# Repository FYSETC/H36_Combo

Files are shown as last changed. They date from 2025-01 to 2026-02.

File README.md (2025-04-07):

# H36_Combo
H36 Combo V1 is a newly designed 125℃ high temperature tool board Based on STMG0B1T3.

> [!IMPORTANT] 
>- Since there is no 125 degree Celsius USB-HUB chip, the 125 degree Celsius operating environment is limited to CANBUS mode；
>- Klipper currently does not support 125 degree Celsius accelerometers, so the 125 degree Celsius operating environment does not include accelerometers. The default version of H36 is ADXL345, which has a maximum operating temperature of 85 degrees Celsius. The 105 degree Celsius ADXL345-EP version is optional, but it is more expensive.

V1.1

1.add Driver NTC

2.add 3.3V/5v monitor

3.add 24v monitor

\-------------------------------------

V1.2

1.change to XT30

2.add reserve protection

3.fix can/usb indicate

\-------------------------------------

V1.3 (Currently Available)

> [!NOTE]
> V1.3 only makes hardware changes and does not affect any software configuration.

1.Add level_shift to FAN_TACH

2.Fix silk mark

3.Add jumper resistor from USB-C to STM32

4.ADXL345-EP optional

5.Change the LDO chip to TLV75733

6.New mass-produced cables（Mold Forming）

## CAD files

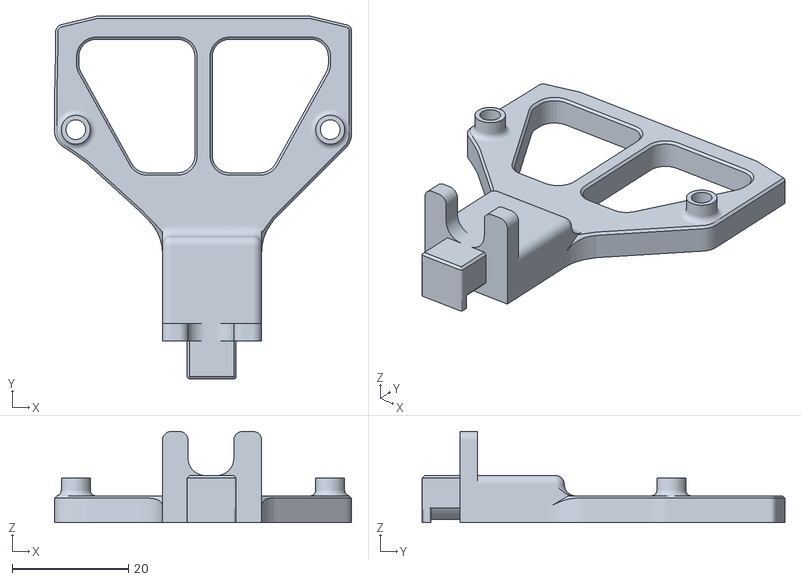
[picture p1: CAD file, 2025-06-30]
STL/H36_MainMount_FYS_Assembly.STL
51.2 x 62.5 x 15.7

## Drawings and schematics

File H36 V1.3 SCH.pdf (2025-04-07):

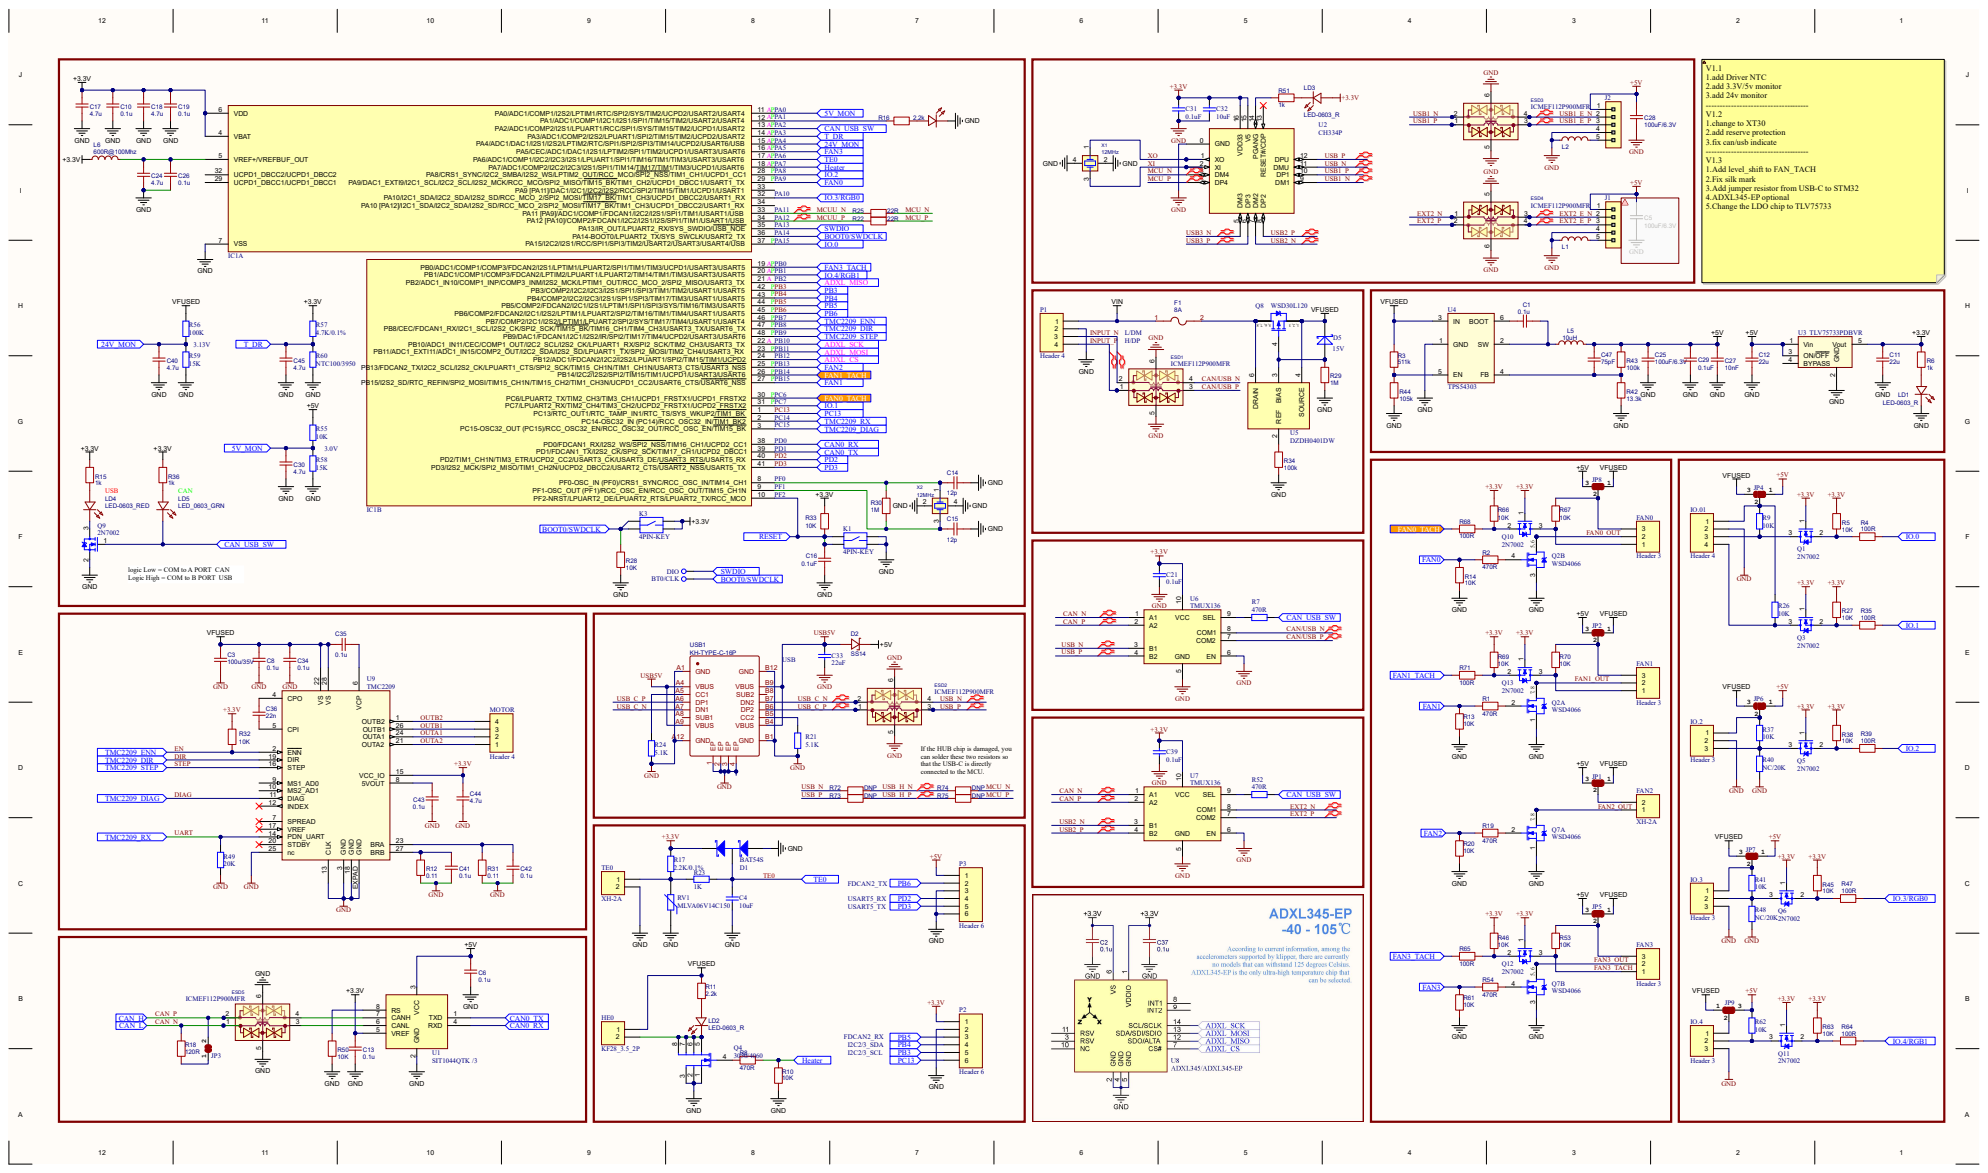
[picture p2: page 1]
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

logic Low = COM to A PORT CAN
Logic High = COM to B PORT USB

If the HUB chip is damaged, you
can solder these two resistors so
that the USB-C is directly
connected to the MCU.

According to current information, among the

accelerometers supported by klipper, there are currently
no models that can withstand 125 degrees Celsius.
ADXL345-EP is the only ultra-high temperature chip that

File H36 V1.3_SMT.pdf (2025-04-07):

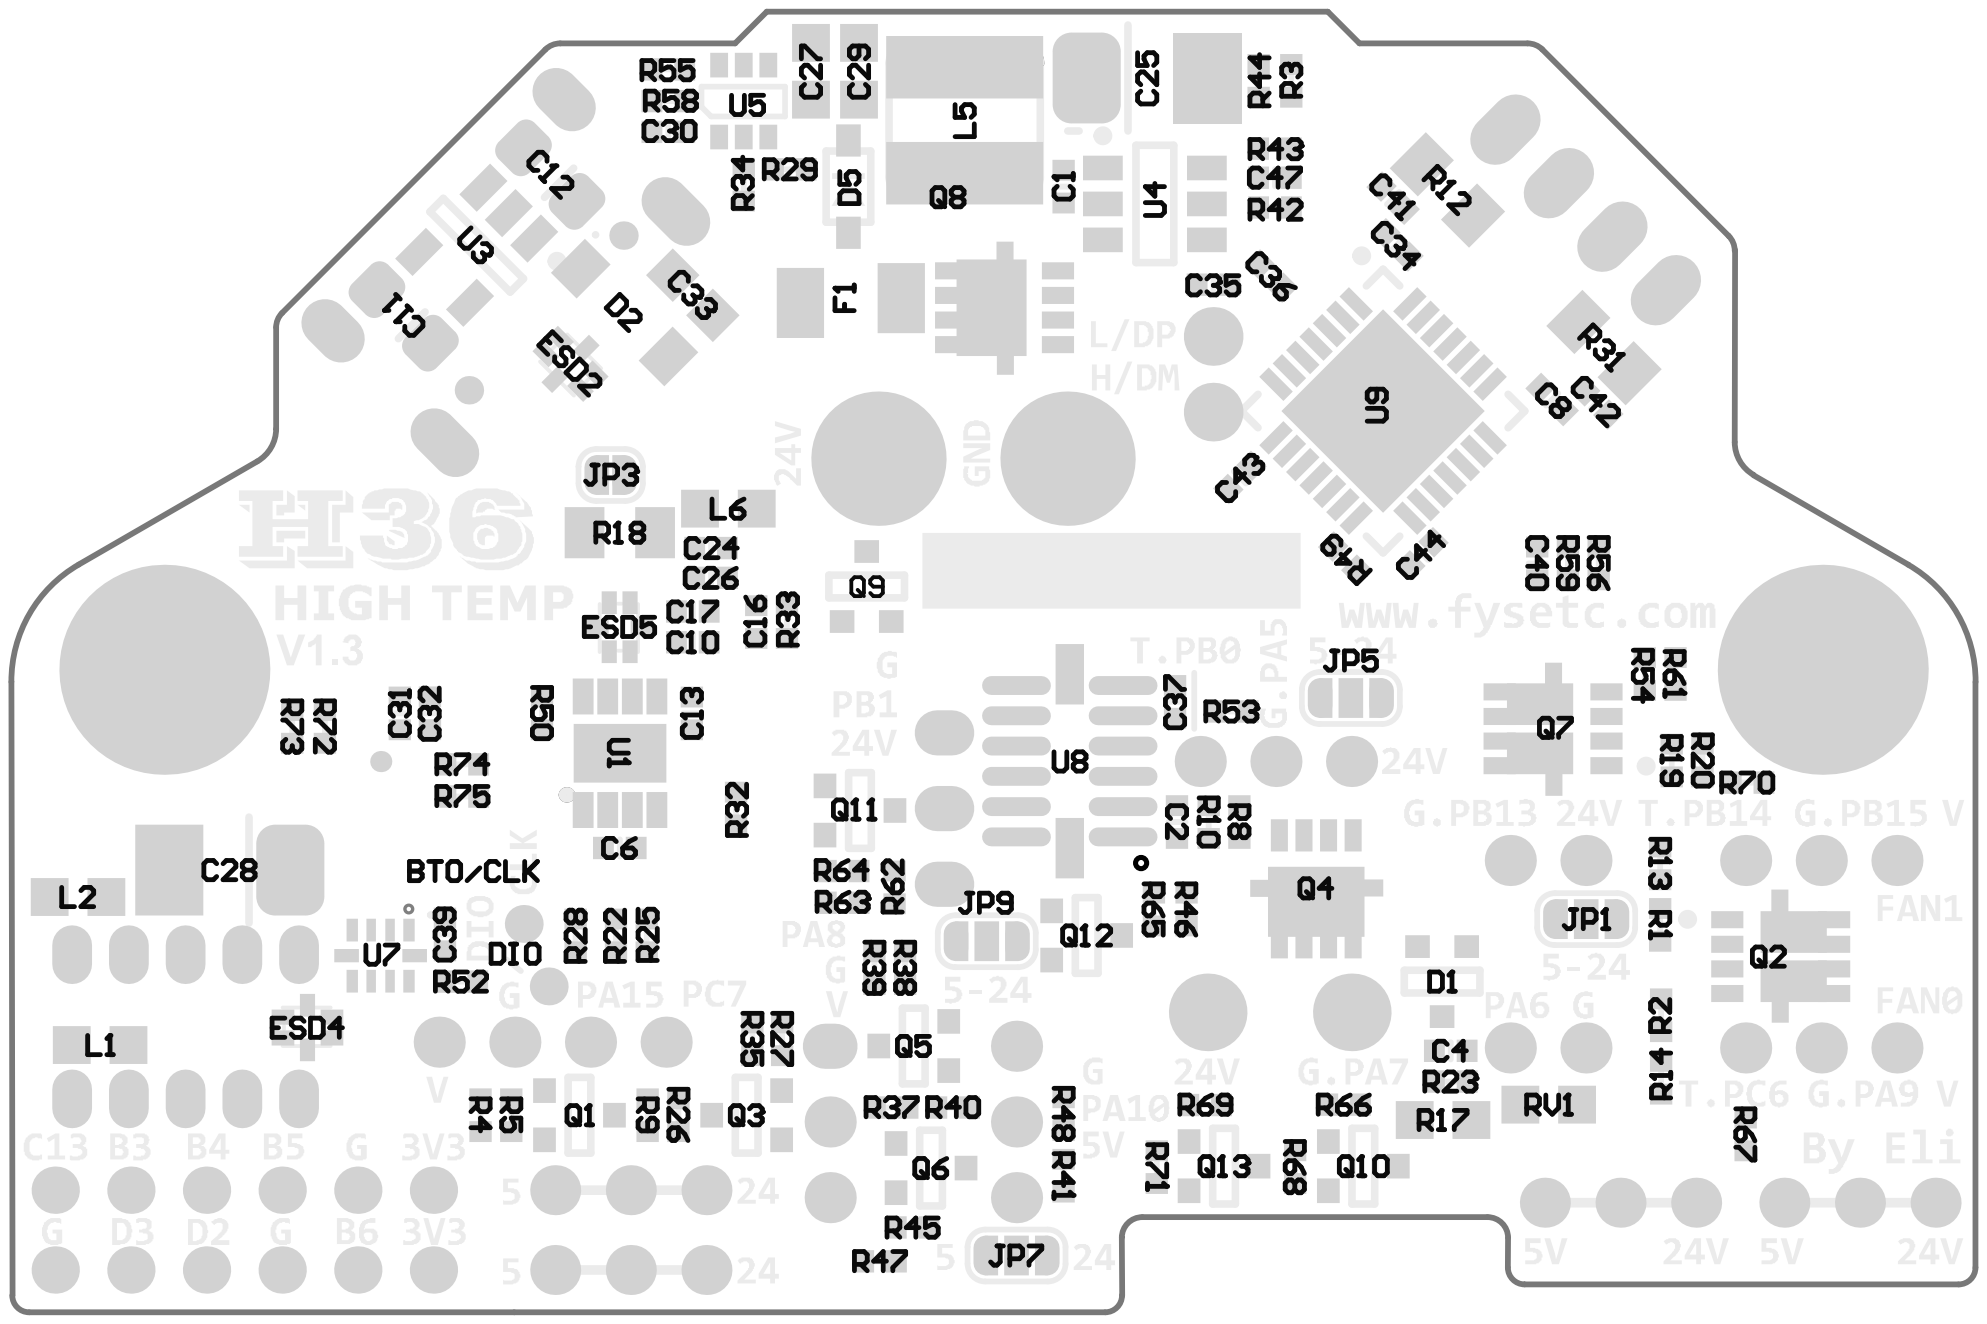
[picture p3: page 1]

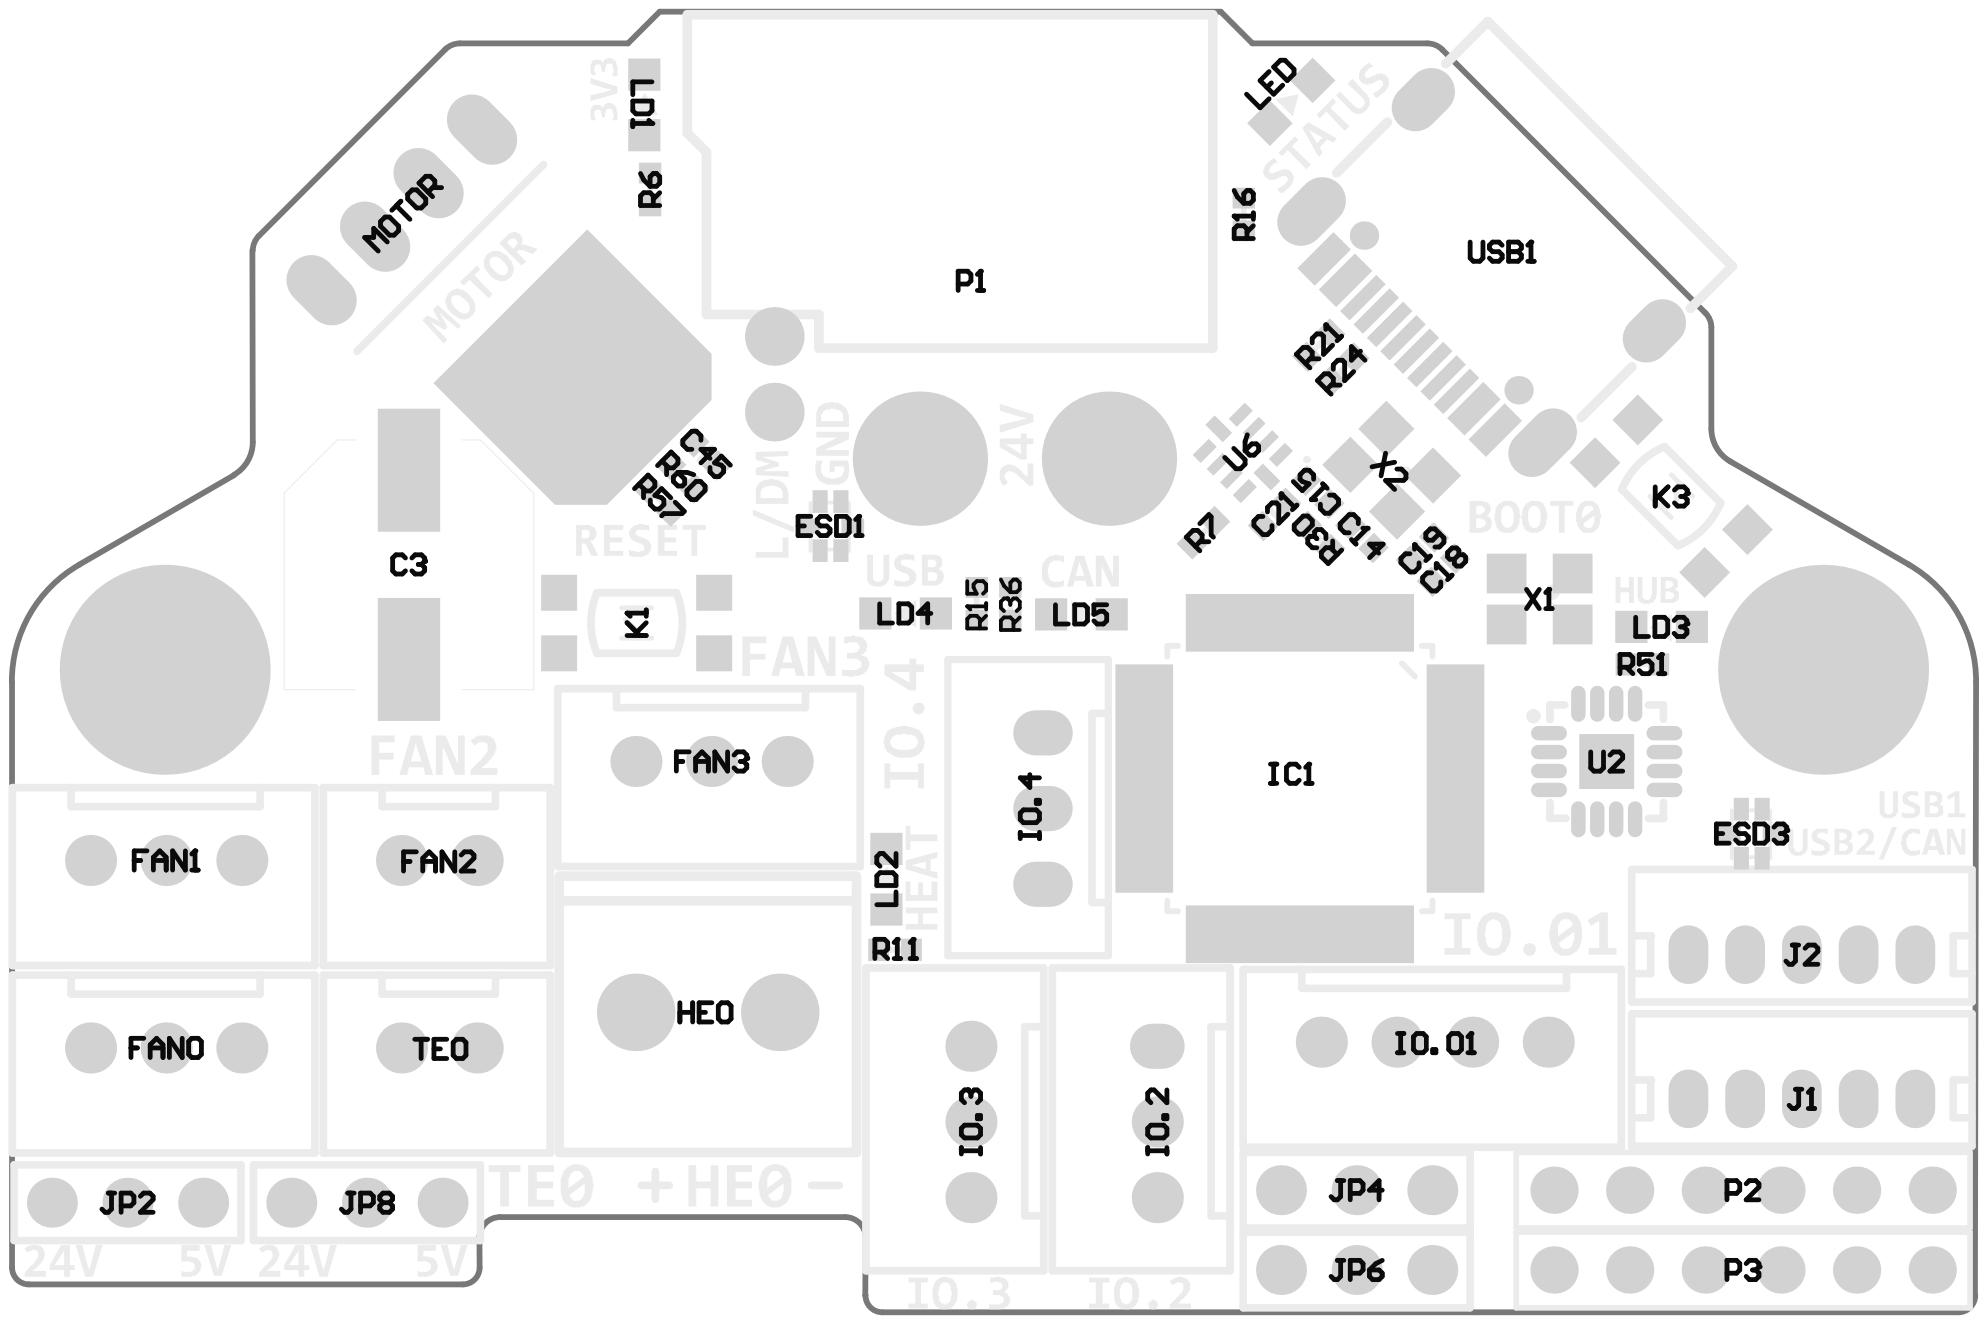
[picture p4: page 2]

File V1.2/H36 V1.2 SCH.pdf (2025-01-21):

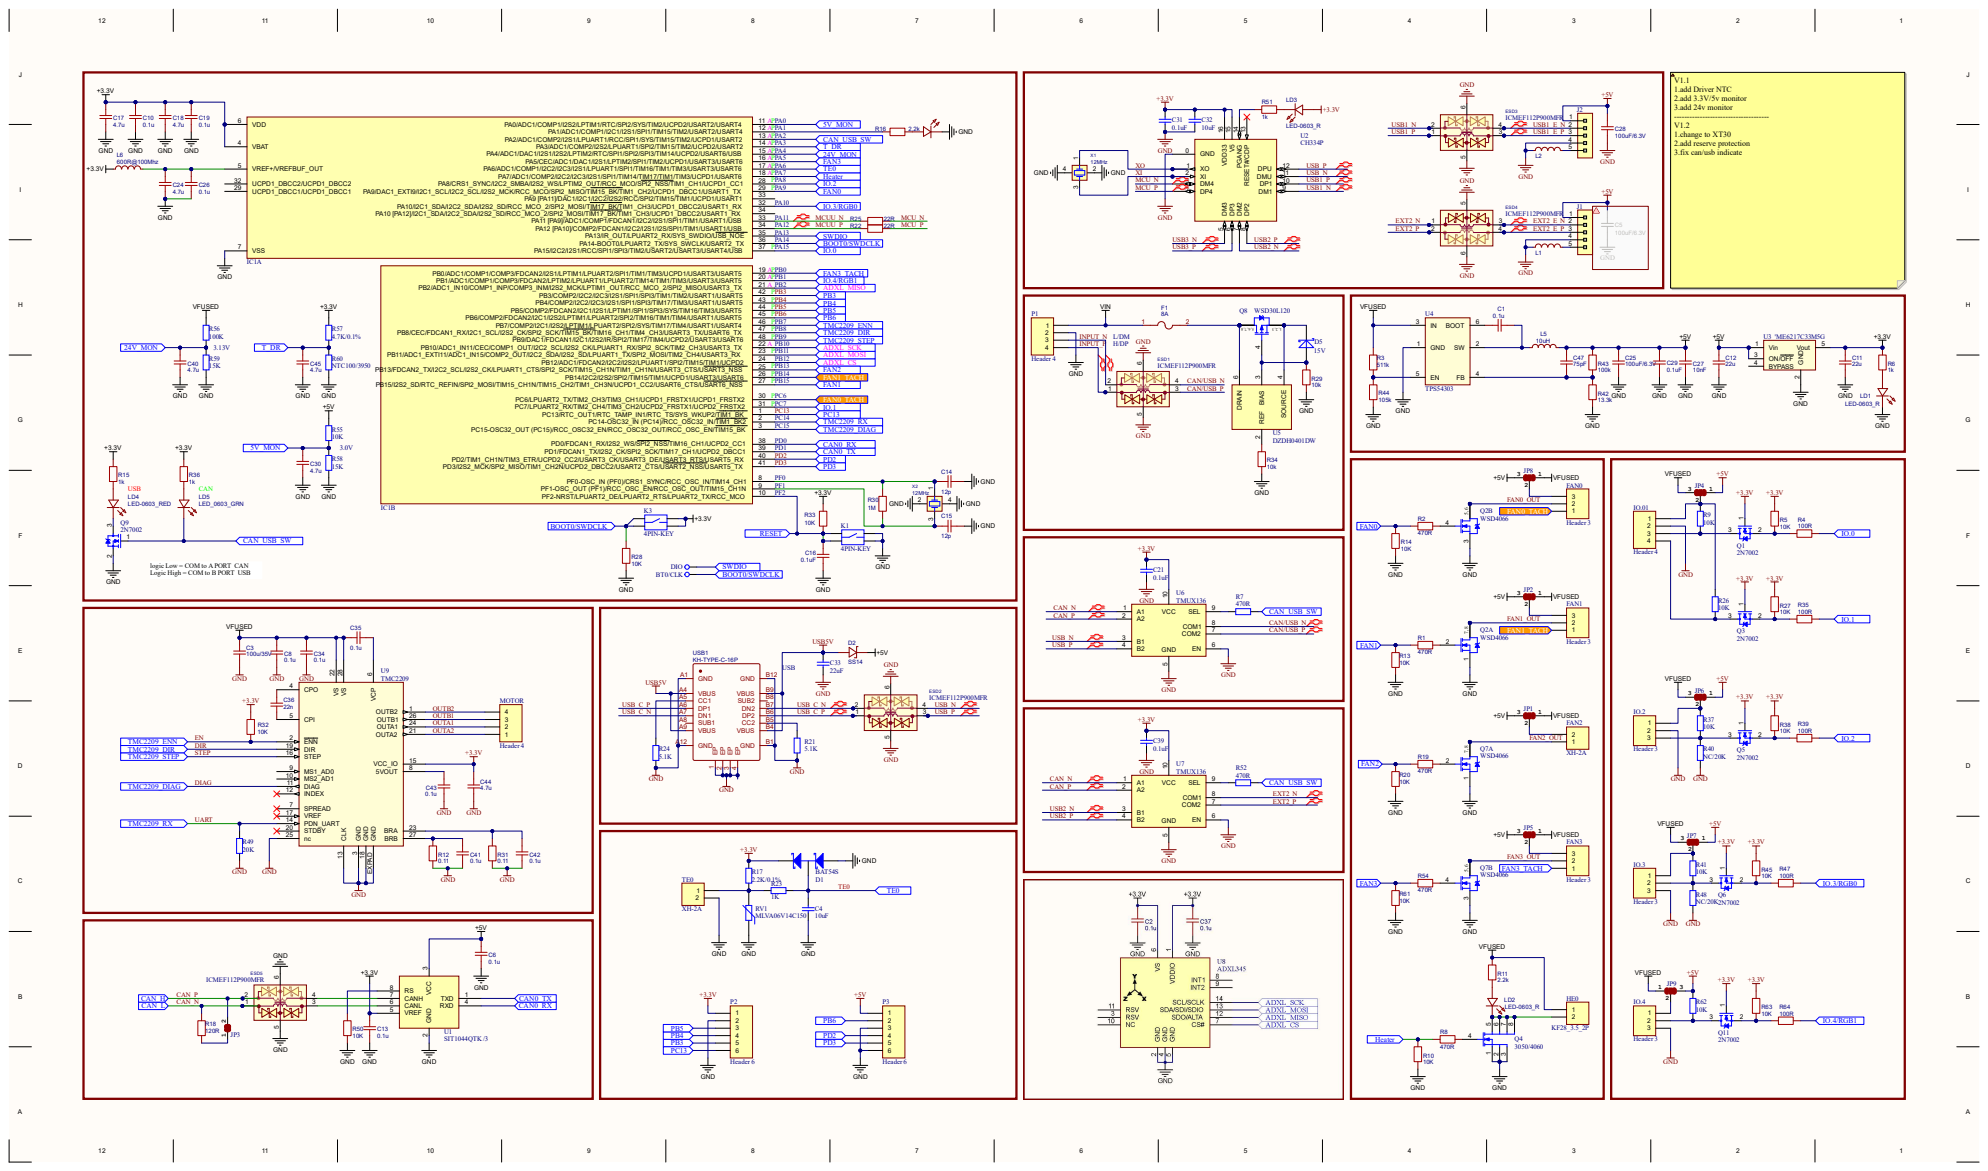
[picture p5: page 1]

1.change to XT30
2.add reserve protection
3.fix can/usb indicate

logic Low = COM to A PORT CAN
Logic High = COM to B PORT USB

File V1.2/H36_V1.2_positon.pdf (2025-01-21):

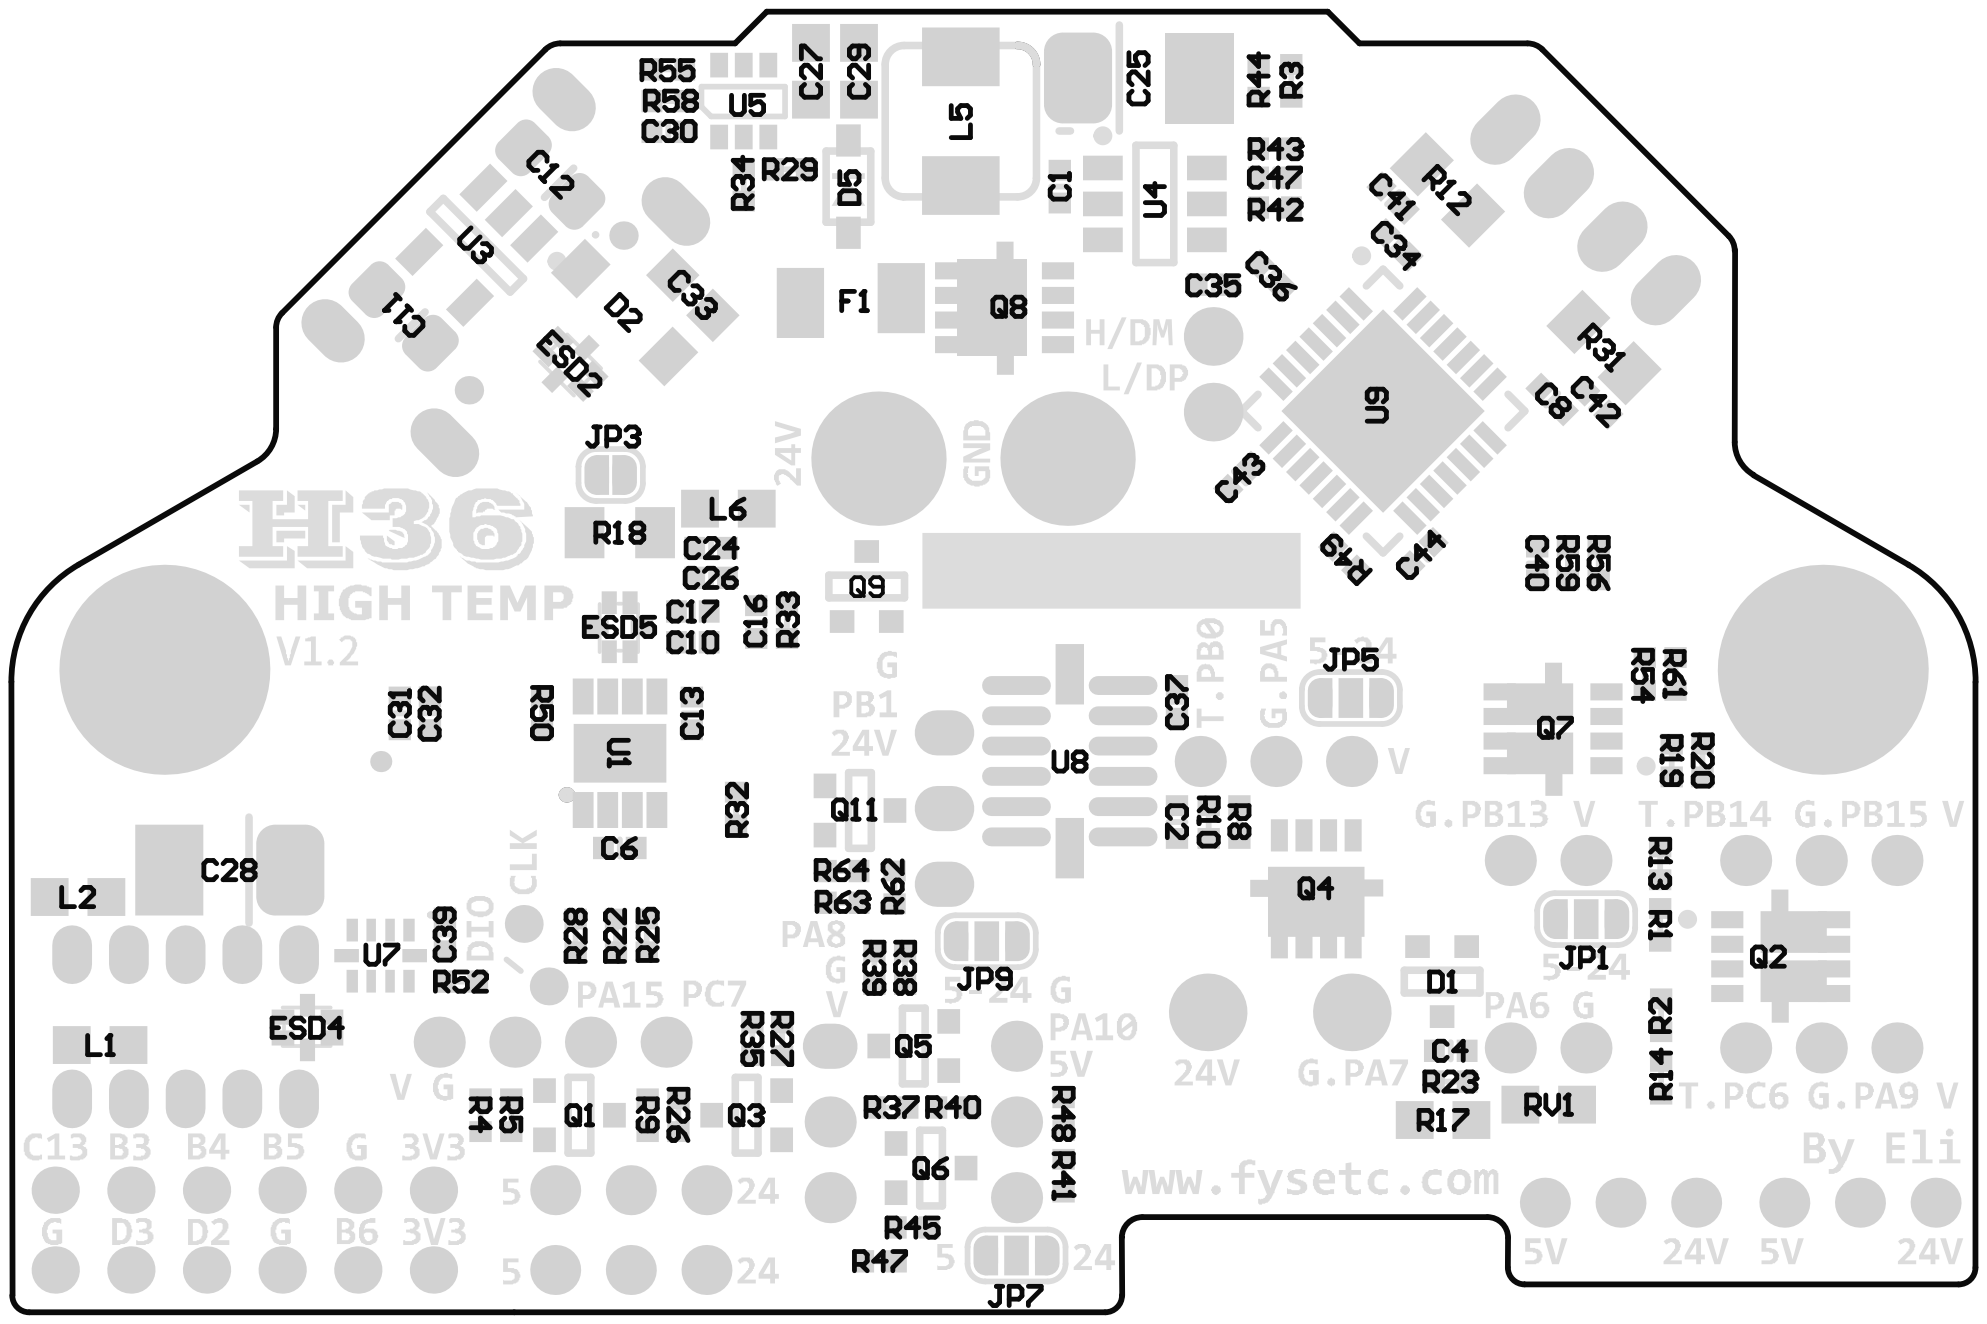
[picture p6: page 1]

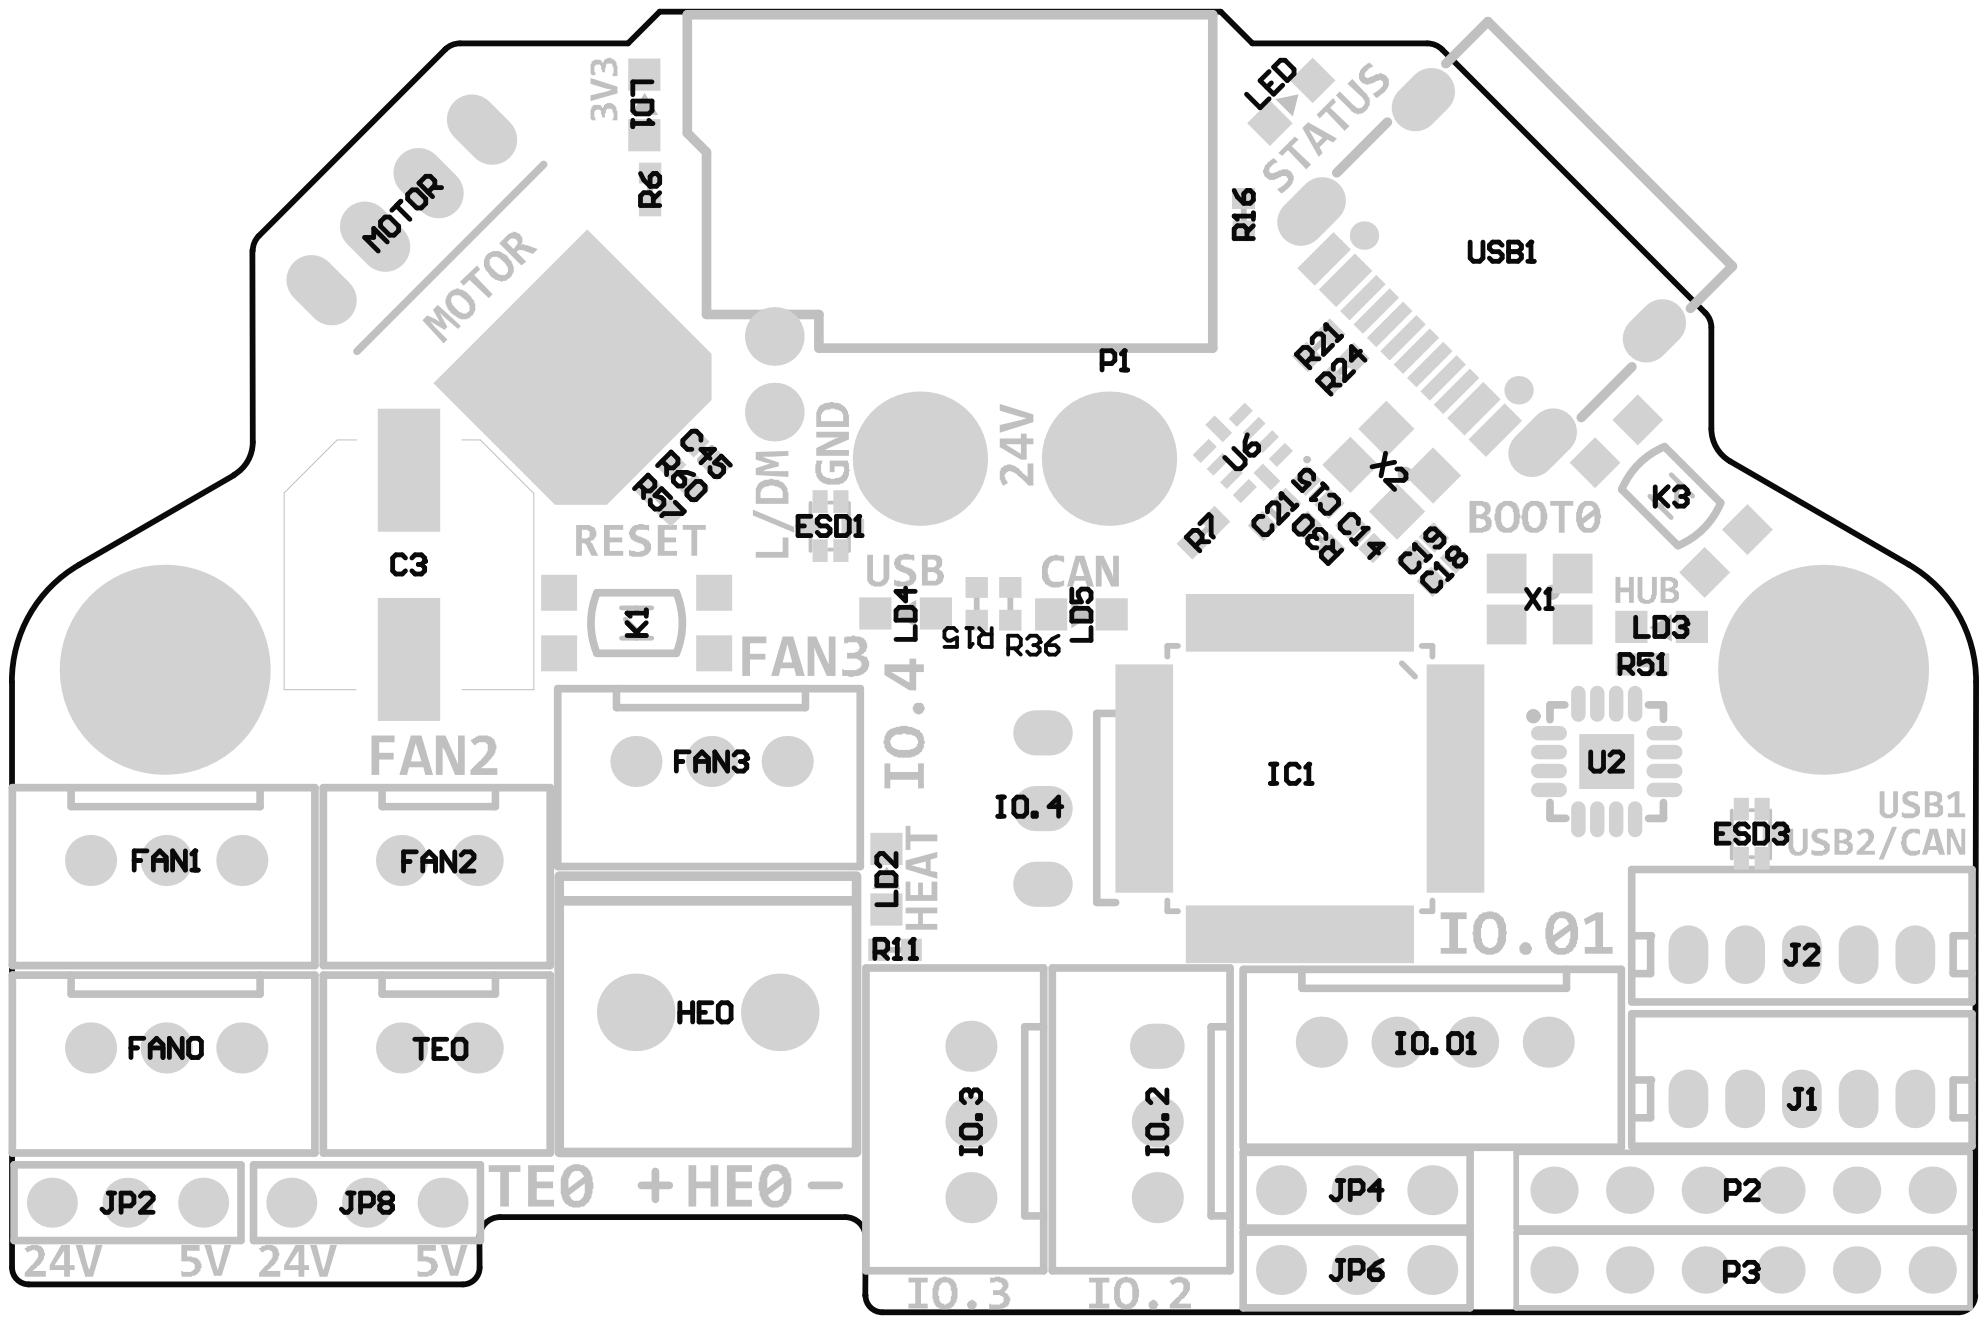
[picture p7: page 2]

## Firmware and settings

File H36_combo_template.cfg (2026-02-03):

[mcu H36_combo]
#serial: /dev/serial/by-path/*
#serial: /dev/serial/by-id/*
#canbus_uuid=e185794c4226

# CAN_RX: PD0
# CAN_TX: PD1
# CAN USB switch: PA2
# logic Low = COM to A PORT  CANBUS 
# Logic High = COM to B PORT  USB

#####################################################################
# Extruder
#####################################################################

[extruder]
step_pin: H36_combo:PB9 
dir_pin: H36_combo:PB8
enable_pin: !H36_combo:PB7

##  Update value below when you perform extruder calibration
##  If you ask for 100mm of filament, but in reality it is 98mm:
##  rotation_distance = <previous_rotation_distance> * <actual_extrude_distance> / 100
##  22.6789511 is a good starting point for Bondtech 5mm gears
##  34.37086 for Bondtech 8mm gears (Galileo)
rotation_distance: 4.45   #22.6789511   #Bondtech 5mm Drive Gears
##  Update Gear Ratio depending on your Extruder Type
##  Use 50:17 for Afterburner/Clockwork (BMG Gear Ratio)
##  Use 80:20 for M4, M3.1
##  Use 7.5:1 for Galileo
##  gear_ratio: 50:10               #for Stealthburner/Clockwork2 BMG Gear Ratio
microsteps: 16
full_steps_per_rotation: 200    #200 for 1.8 degree, 400 for 0.9 degree
nozzle_diameter: 0.400
filament_diameter: 1.75
heater_pin: H36_combo: PA7 
pullup_resistor: 2200
## Check what thermistor type you have. See https://www.klipper3d.org/Config_Reference.html#common-thermistors for common thermistor types.
## Use "Generic 3950" for NTC 100k 3950 thermistors
sensor_type: Generic 3950
sensor_pin: H36_combo:PA6 
min_temp: -273.15 #1 #-273.15 
max_temp: 360 #360 
max_power: 1.0
min_extrude_temp: -273
control = pid
pid_kp = 26.213
pid_ki = 1.304
pid_kd = 131.721
##  Try to keep pressure_advance below 1.0
#pressure_advance: 0.02 #0.05
##  Default is 0.040, leave stock
#pressure_advance_smooth_time: 0.040
max_extrude_cross_section: 5000.0

[tmc2209 extruder]
uart_pin: H36_combo:PC14
interpolate: false
run_current: 0.7
sense_resistor: 0.110
stealthchop_threshold: 0
#diag_pin: H36_combo:PC15

#####################################################################
# Input Shaper
#####################################################################

[adxl345]
cs_pin: H36_combo:PB12
spi_software_sclk_pin: H36_combo:PB10
spi_software_mosi_pin: H36_combo:PB11
spi_software_miso_pin: H36_combo:PB2
axes_map: -y,z,-x

[resonance_tester]
accel_chip: adxl345
probe_points:
    300,300,30 # an example

#####################################################################
# FANS
#####################################################################

[fan_generic fan0]
pin: H36_combo:PA9
max_power:1.0
shutdown_speed:0.0
cycle_time:0.5
hardware_pwm:false
kick_start_time:0.10
off_below:0.1
tachometer_pin: H36_combo:PC6
# Please make sure the feedback level does not exceed 5V!
#tachometer_ppr:
#tachometer_poll_interval:

[fan_generic fan1]
pin: H36_combo:PB15
max_power:1.0
shutdown_speed:0.0
cycle_time:0.5
hardware_pwm:false
kick_start_time:0.10
off_below:0.1
tachometer_pin: H36_combo:PB14
# Please make sure the feedback level does not exceed 5V!
#tachometer_ppr:
#tachometer_poll_interval:

[fan_generic fan2]
pin: H36_combo:PB13
max_power:1.0
shutdown_speed:0.0
cycle_time:0.5
hardware_pwm:false
kick_start_time:0.10
off_below:0.1

[fan_generic fan3]
pin: H36_combo:PA5
max_power:1.0
shutdown_speed:0.0
cycle_time:0.5
hardware_pwm:false
kick_start_time:0.10
off_below:0.1
tachometer_pin: H36_combo:PB0
# Please make sure the feedback level does not exceed 5V!
#tachometer_ppr:
#tachometer_poll_interval:

#####################################################################
#	Mcu & Driver Temperature
#####################################################################

[temperature_sensor can_mcu_temp]
sensor_type: temperature_mcu
sensor_mcu: H36_combo
min_temp: 0
max_temp: 150

[temperature_sensor Driver_Temp]
sensor_type: Generic 3950
sensor_pin: H36_combo: PA3
min_temp:0
max_temp:150

#####################################################################
#	Voltage Monitor
#####################################################################

[adc_temperature 5V_Monitor]
temperature1: 5
voltage1: 3.0
temperature2: 4
voltage2: 2.4
temperature3: 3
voltage3: 1.8

[adc_temperature 24V_Monitor]
temperature1: 24
voltage1: 3.13
temperature2: 22
voltage2: 2.87
temperature3: 21
voltage3: 2.74

[temperature_sensor 5V_Monitor]
sensor_type: 5V_Monitor
sensor_pin: H36_combo:PA0   #5V_MON
adc_voltage: 3.3
voltage_offset: 0

[temperature_sensor 24V_Monitor]
sensor_type: 24V_Monitor
sensor_pin: H36_combo:PA4   #24V_MON
adc_voltage: 3.3
voltage_offset: 0


#####################################################################
#	I/O
#####################################################################

# IO.0: PA15
# IO.1: PC7 
# IO.2: PA8
# IO.3/RGB0: PA10
# IO.4/RGB1: PB1

#####################################################################
#	RGB
#####################################################################

[neopixel sb_leds]
pin: H36_combo:PA10 #IO.3/RGB0
chain_count: 10
color_order: GRB, GRB, GRB, GRB, GRB, GRB, GRB, GRB, GRBW, GRBW
initial_RED: 0.5 
initial_GREEN: 0.5
initial_BLUE: 0.5
initial_WHITE: 0.5

[neopixel ext_leds]
pin: H36_combo:PB1 #IO.4/RGB1
chain_count: 1
color_order: GRB
initial_RED: 0.5
initial_GREEN: 0.5
initial_BLUE: 0.5
initial_WHITE: 0.5
